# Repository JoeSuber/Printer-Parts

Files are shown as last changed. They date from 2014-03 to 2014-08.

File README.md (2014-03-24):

Printer-Parts
=============

Parts and set-up files for my own functioning 3D-printer design:

Why another 3D printer? Here are the reasons for this one:

1) utilize bargain priced salvaged nema-23 stepper motors, get higher torque/$ and 1/32 micro-steps.

nema-23 motors are mostly bigger, torque-ier, and consequently can draw more current than this job really requires - but they often have a better dollar-per-Newton ratio than the nema-17 motors one usually sees in 3D printers.  I have opportunistically purchased 25 or so for under $10 per and only had to pound the sintered cog-wheel off the shaft to obtain a great, cheap, 4-wire motor. The Pololu stepper drivers that utilize the Texas Instruments chip run cooler and allow 1/32 micro-stepping with a higher top current.  The only downside to that TI driver is a longer minimum pulse than the Allegro chip, but at 1.6 micro-seconds it has never been an issue, even with very small diameters.  Which brings me to the 2nd reason:

2) Get rid of belts and sprockets.

Printed sprockets and mismatched belts are the source of many errors and dreaded backlash.  I think everyone using belts eventually wants to use metal wheels that fit their printer design perfectly.  That cannot help but be another source of expense as we must search out particular diameters, tooth-designs, and shafting. Getting belt tension and return idler wheels to work perfectly without spending for the proper bearings and hardware is another headache we can do without.  The Delta-Bots have shown the wonders of Spectra fishing-line as a transmitter of force. However, I suspect the Delta-Bot works best as a prefab kit - and all the good ones use those carbon-fiber rods which I just don't have laying around. Delta is out. My local hardware store has hobby brass tube that can become 5 or 6 drive-spools for $3.  Idlers can be just about any bearing with some printed cones stuck on the outside to nudge the line on centre.  The headaches don't go away completely, but the diameters are small and the wheels are round. And you learn some fishing knots.

3) direct-drive extruder = fewer headaches, better filament retraction. 

I do eventually want to build a Delta-Bot - they look really neat.  But I suspect the Bowden-tube to the hot-end is not ideal unless filament and PTFE are well-matched and the PTFE is not bulged or worn anywhere along its length.  Also, that PTFE tube is another mail-order-only item.  Sure, I am throwing a lot more mass around by having the extruder motor on the X-carriage, but remember we have the Nema-23 torque and the 5/16 inch diameter drive spool to do the hurky-jerks we need on that mass.  Also, it is cheap and easy to switch between 3mm and 1.75mm filament with this set-up.  The filament drive is chosen to use a 608zz bearing and mk7+ gear, which I think is the best price-performance available.  Wade's + hobbed-bolts don't seem to be worth the extra headaches except to the Rep-Strap purist.

4) Benefit from Prusa-Mendel ubiquity, while avoiding some pitfalls.

This design owes a lot to the Prusa-I3 and Mendel lineage. I think it is naturally stiffer and depending on your skill-set, easier to build.  A low center of gravity and wide base reduce harmonic vibrations.  Y-axis drive is centrally located with no idler. Z-rods are moved off the stepper top-surface so they don't vibro-dance, instead forming a stiffer truss with the 1/4" Z-screw. Canted square-tubes dampen X-wobbles by compressing or tensioning horizontal rods instead of torqueing 90 degree joints.  More of this design is in imperial sizes available at your local North-American Home-Depot or Ace-Hardware.  It isn't as compact, because I like to be able to reach everything.  It isn't as pretty for the same reason.  Aluminium square tube and C-channel are cheaper and easier to cut than maker-beam / t-slot. The smooth-rod lengths are such that you may order 1 long rod, cut it in half (Dremmel, not hacksaw) for each pair.  Linear Bearings are cheap if you stick to LM8UU.  I do believe the LM12UU rod on the Y axis is worth the extra money, as it is acting structurally as well. You have multiple ways to trim and level this as you build. One long 5/16" threaded rod can be cut into all the needed sections, and 1/4" bolts & rod cover most everything else that isn't M3.  Using Sanguinolu as the brains, Marlin Firmware settings for Mendels or Ultimakers will get you most of the way there, just remember to compute the proper (likely much higher) steps - per - millimetre for each axis.  I am not sure why RAMPS 1.x + Arduino Mega2560 are more popular in year 2014 as that combo seems more expensive than Sanguinolu when I add it up - but this design should have no problem using RAMPS or some future ARM based solution which will surely be Prusa-Mendel compatible.

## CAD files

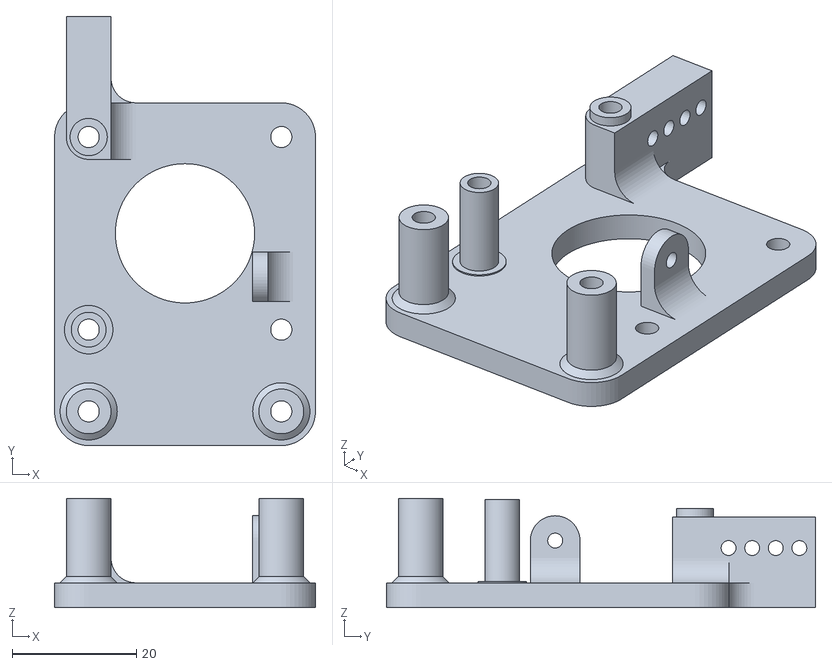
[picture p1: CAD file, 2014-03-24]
ArmDriveSTL/ADBaseMK7.stl
42.0 x 69.0 x 17.6

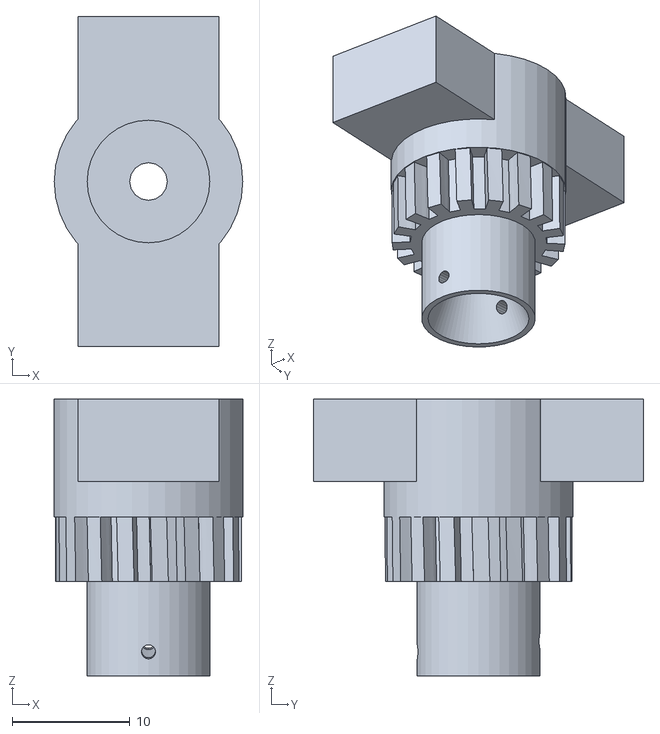
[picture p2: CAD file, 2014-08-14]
x-carriage_thread_plug_14mm.stl
16.0 x 28.0 x 23.5

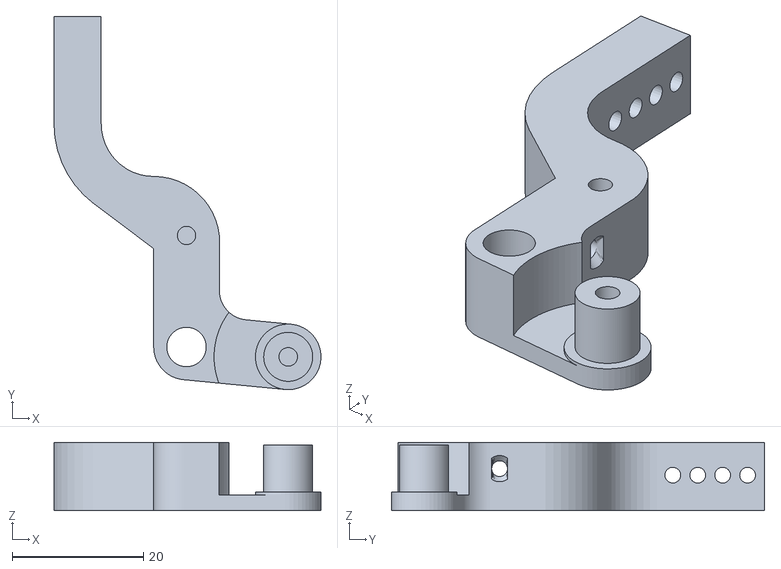
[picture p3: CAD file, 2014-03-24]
ArmDriveSTL/ADLowerArmMK7.stl
40.7 x 56.9 x 10.4

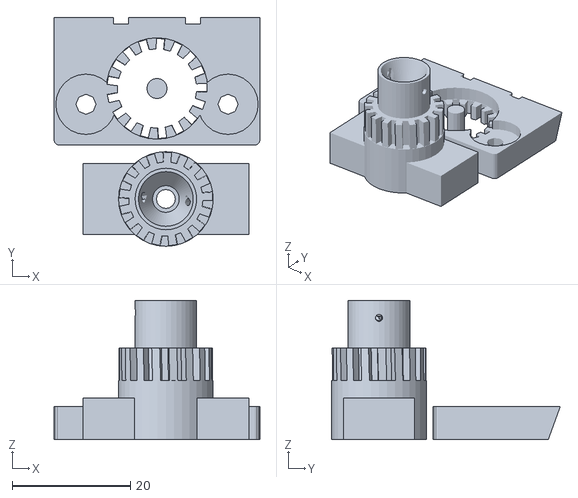
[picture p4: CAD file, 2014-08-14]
x-carriage_thread_plug_hex_only.stl
34.8 x 38.6 x 23.5

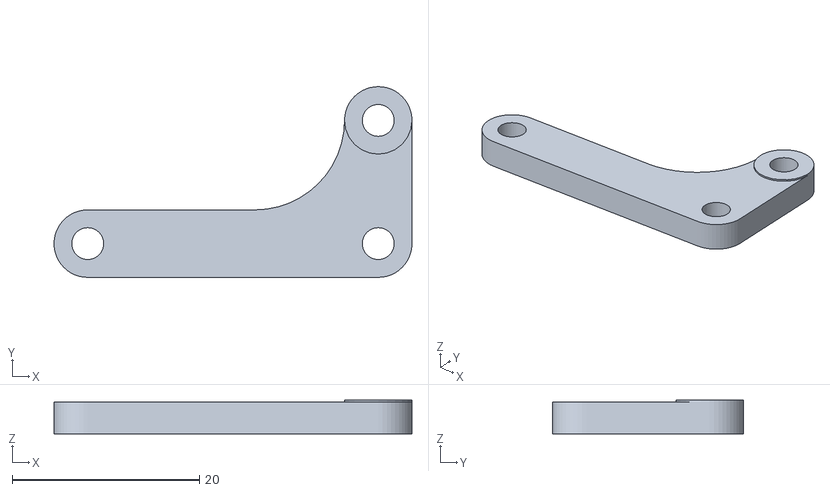
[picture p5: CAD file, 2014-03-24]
ArmDriveSTL/ADTopMK7.stl
38.2 x 20.4 x 3.60

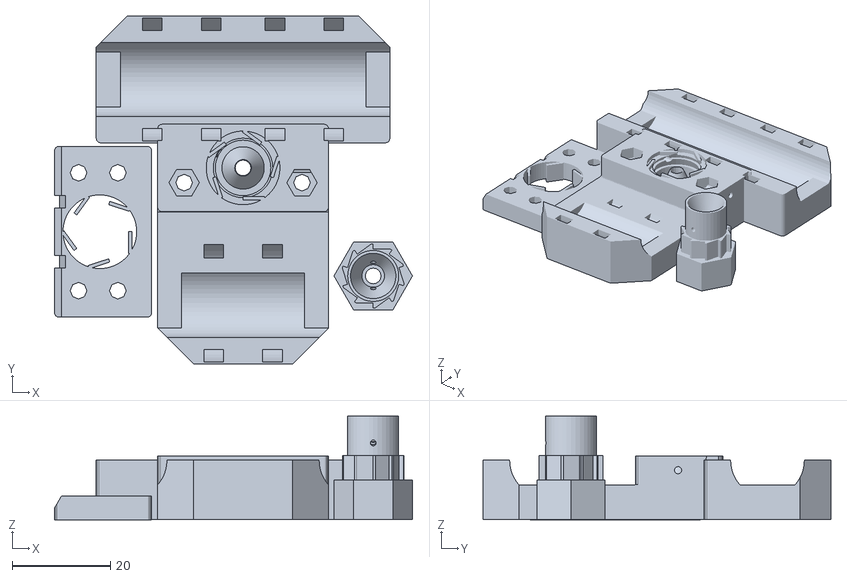
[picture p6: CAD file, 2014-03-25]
x-carriage_for_thread.stl
72.9 x 70.8 x 21.1

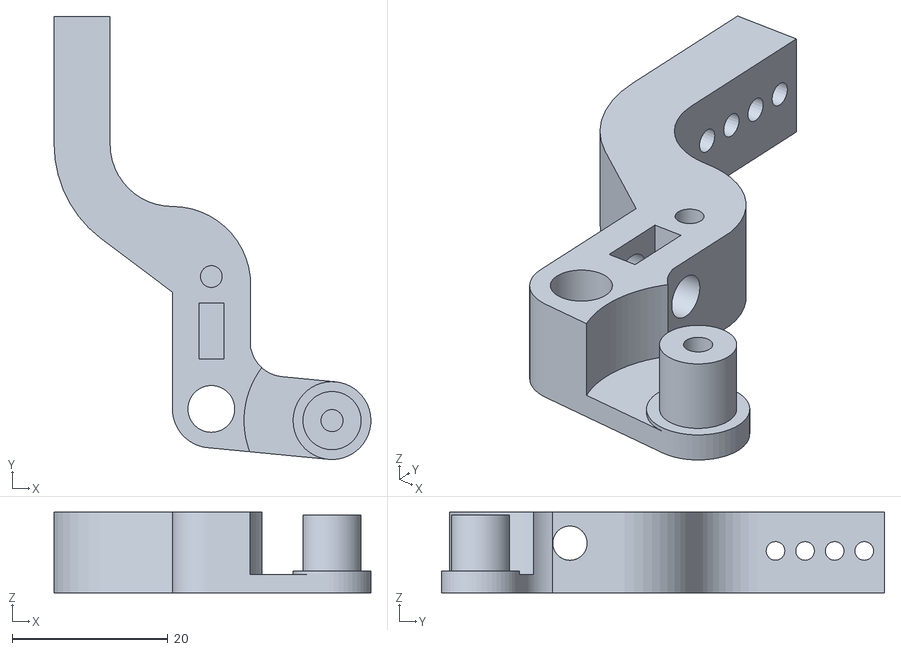
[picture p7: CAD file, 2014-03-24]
ArmDriveSTL/ADLowerArmAltMK7.stl
40.7 x 56.9 x 10.4

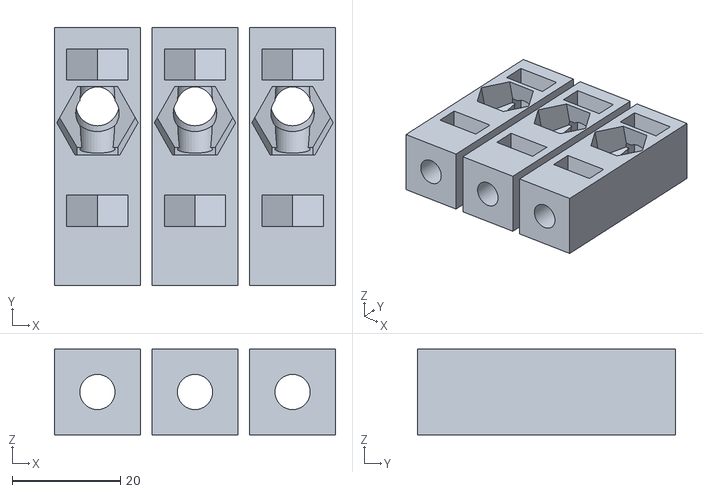
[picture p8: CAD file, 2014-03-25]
bar_rod_joinx2.stl
51.9 x 47.5 x 15.9

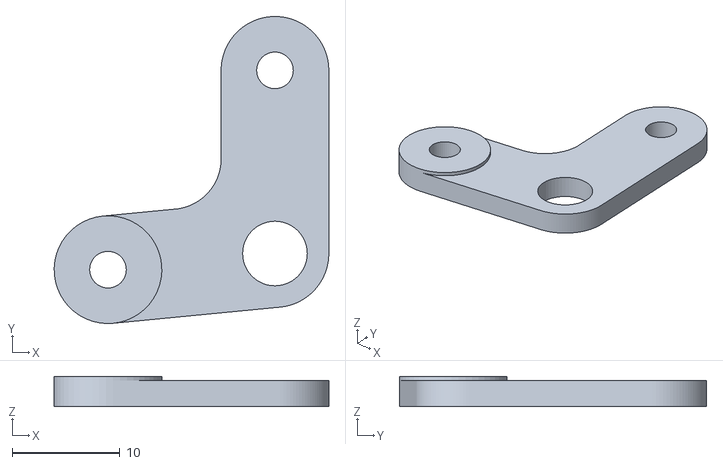
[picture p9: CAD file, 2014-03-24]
ArmDriveSTL/ADUpperArmMK7.stl
25.5 x 28.5 x 2.80

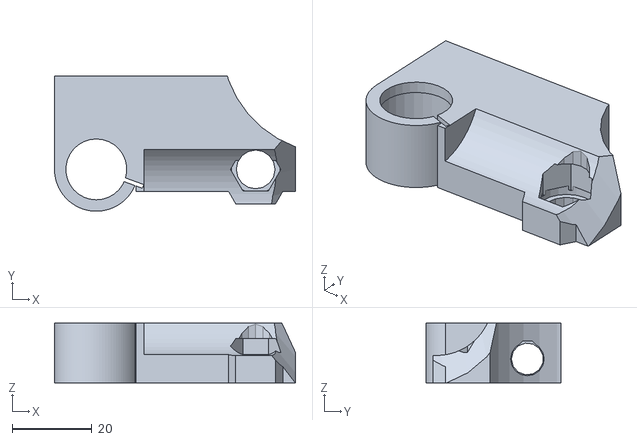
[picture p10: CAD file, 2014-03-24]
top_stabilizer_mirror.stl
60.5 x 34.0 x 15.0

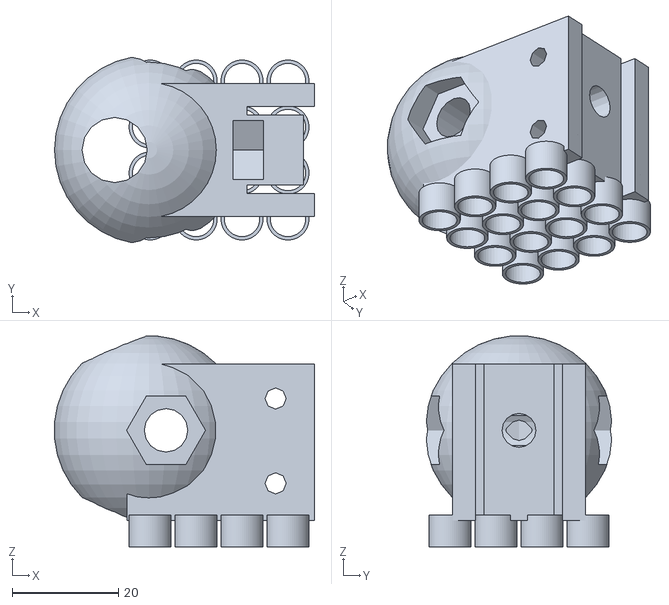
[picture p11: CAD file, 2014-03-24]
bars_bits_on_base.stl
49.0 x 34.9 x 39.8

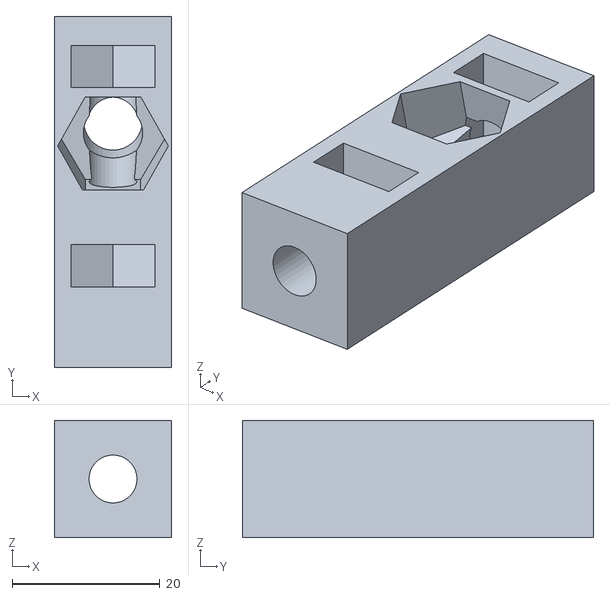
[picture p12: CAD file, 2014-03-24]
bar_to_rod_join.stl
15.8 x 47.5 x 15.9

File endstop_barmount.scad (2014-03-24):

// attach things to base...

use <./Abar.scad>

cB=25;
tubeXY = 19.25;
swX = 20.5;
swY = 10.3;
swZ = 6.5;
wireThick = 3.1;
wireZ = 3.65;
wire1 = 1.11;
wire2 = 11.38;
wire3 = 18.5;
leverHinge = 3.4;
leverExtends = 19.35;
hole1X = 5.15;
hole2X = 14.67;
holeY = 2.78;
holeRad = 2.5/2;
sur = 1.56;
totalX = sur*2 + swX;
totalY = sur + swY;
totalZ = swZ + sur;
posX = totalX/2;
posY = totalY/2 + sur/2;
posZ = totalZ/2;
groove= 1.75;
pH = 30;
Ang = 12.7;

module switch(){
	cube([swX,swY,swZ], center=true);
	translate([0 ,-posY,-.1])
		cube([wire3, 3+2+.1, wireZ+.1], center=true);
}

module switchbox(){
	difference(){
		union(){
		translate([totalX/2,totalY/2,totalZ/2])
			cube([totalX,totalY-.1,totalZ], center=true);			
		}
		translate([posX,posY,posZ])
			switch();
	}
}

module aluTube(){
	cube([tubeXY,tubeXY, pH+.1], center=true);
	translate([tubeXY/2+.1, 0, 0])
		cylinder(r=groove, h=pH+.1, center=true, $fn=16);
	translate([tubeXY/2+.1, tubeXY/3, 0])
		cylinder(r=groove, h=pH+.1, center=true, $fn=16);
	translate([tubeXY/2+.1, -tubeXY/3, 0])
		cylinder(r=groove, h=pH+.1, center=true, $fn=16);
	hull(){
	translate([-tubeXY/2 - sur*2+.2, 0, -pH]) rotate([0,-90,0])
		cylinder(r1=tubeXY/2-2, r2=tubeXY/2+sur*4-2, h=sur*4+.1, center=true);
	translate([-tubeXY/2 - sur*2+.2, 0, pH]) rotate([0,-90,0])
		cylinder(r1=tubeXY/2-2, r2=tubeXY/2+sur*4-2, h=sur*4+.1,center=true);
		}
}

module plasticTube(cH=3){
	minkowski(){
	cube([tubeXY+sur*4,tubeXY+sur, cH], center=true);
	cylinder(r=1.2, h=cH, $fn=48, center=true);
	}

}

module holderclip(){
	difference(){
	plasticTube();
	aluTube();
	}
}

module placeBox(){
	translate([-totalX/2-(pH/2*sin(Ang)-sur-.2),tubeXY,0]) rotate([90,Ang,0])
		switchbox();
}
holderclip();

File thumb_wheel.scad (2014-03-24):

// *******************************************************
// *   Parametric thumb wheel                            *
// *   by Chris Garrett                                  *
// *   20-nov-2011                                       *
// *   Small changes by Juan Gonzalez-Gomez (Obijuan)    *
// *   31-Aug-2012                                       *
// *******************************************************


// *** Configuration variables ***
wheel_d = 12;    // Outer Diameter of the thumb wheel
wheel_h = 3;     // Height of the thumb wheel
hole_d = 3.2;    // Diameter of center hole
hex_sz = 6.4;      // Size of the hex (nut trap)
                 // An M4 nut fits perfectly in a 7mm hex opening made on my Prusa
hex_d = 2;       // Depth of the hex (set this < or = to wheel_h)
knurl_cnt = 8;  // Number of cutouts around the wheel
knurl_d = 3;     // Diameter of the cutouts

//-- drills
drill_M3 = 3.2;

//-- captive Nuts
nut_h = 2.2;
nut_radius = 6.4/2;


// *** Code area ***

// The thumb wheel 

difference() {
  //-- Base cylinder
  cylinder(h=wheel_h, r=wheel_d/2, $fn=50);

  //-- Cutouts
  for(i = [0:knurl_cnt-1]) {
   rotate(v=[0,0,1], a=i*360/knurl_cnt) 
     translate([0,wheel_d/2+knurl_d/4,-1]) 
       cylinder(h=wheel_h+2, r=knurl_d/2, $fn=50);
  }

  //-- Hex nut body
  translate([0,0,wheel_h-nut_h])
    cylinder(r=nut_radius, h=nut_h+1,$fn=6);

  //-- Hex nut drill
  translate([0,0,-1]) cylinder(h=wheel_h+2, r=hole_d/2, $fn=50);

}

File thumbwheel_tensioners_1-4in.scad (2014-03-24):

include </home/suber1/MCAD/gears.scad>

spread = 12;
teeth = 23;
dp = 1.1;
pi = 3.141592654;
crad = (teeth*dp/pi)/2;
pad = 0.1;	// Padding to maintain manifold
ch = 1;
cr = 17.5;
ct = 2;
r = 3.15;
smooth = 64;	// Number of facets of rounding cylinder

module toroid(){
//difference() {
//	rotate_extrude(convexity=10,  $fn = smooth)
//		translate([cr-ct-r+pad,ct-pad,0])
//			square(r+pad,r+pad);
	rotate_extrude(convexity=10,  $fn = smooth)
		translate([cr-ct-r,ct+r,0])
			circle(r=r,$fn=smooth);
//}
}

module wind_ring(){
difference(){
cylinder(r = crad*2+4, h=2,center=true, $fn=48);
cylinder(r = crad*2+4-2.4, h=2, center=true, $fn=36);
}
}



module thumbwheel(){
difference(){translate([0,0,5]) linear_extrude(height = 8.5, center = true, convexity = 10, twist = 0)
	 //gear(number_of_teeth=21,diametral_pitch=1);
gear(teeth, diametral_pitch=dp, presure_angle=20, clearance=.275);
translate([0,0,5]) rotate([0,90,90]);
	cylinder(r=.66, h= 20, $fn=12, center=true);
translate([0,0,-10]) rotate([180,0,0]);
toroid();
translate([0,0,0]) rotate([0,180,0]);
toroid();
translate([0,0,6.5])
cylinder(r=6.59, h= 6.5, $fn=6, center=true);
//translate([0,0,6])
//wind_ring();
translate([0,0,7])
	cylinder(r=3.25, h= 20, $fn=36, center=true);
// threadhole
translate([0,0,5]) rotate([0,90,90]);
	cylinder(r=.66, h= 20, $fn=12, center=true);
}
}
module fourthumbs(){
rotate([0,180,0]) translate([spread,spread,0])
	thumbwheel();
rotate([0,180,0]) translate([spread,-spread,0])
	thumbwheel();
rotate([0,180,0]) translate([-spread,spread,0])
	thumbwheel();
rotate([0,180,0]) translate([-spread,-spread,0])
	thumbwheel();
}


echo("teeth*pitch/pi/2 =",crad);
fourthumbs();

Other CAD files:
thumbwheels.scad
3_8_to_5_16_inserts.scad
Abar.scad
Alum_Cchan1633x1266.scad
BottomBlock.scad
BottomBlock_top_plate_solo.scad
RatchetLib.scad
SpringSwivvel_LM12UU.scad
SpringSwivvel_LM8UU_3rd.scad
bar_rod_joinx2.scad
bar_to_rod_join.scad
bar_to_rod_longie.scad
bars_bits_on_base.scad
bars_n_bits.scad
bars_n_bits_x3.scad
bars_n_bits_x4.scad
bearing.scad
cylinders.scad
drill_guide_for_alum.scad
endstop_on_C_bar.scad
endstop_ontubeclip.scad
external_gear_script.scad
polyholes.scad
spool_4_shells.scad
spool_idler_x.scad
top_stabilizers.scad
wiremanage_tubeclip.scad
x-carriage_for_thread.scad
x-carriage_thread_plug.scad
x-carriage_thread_plug_14mm.scad
x-carriage_thread_plug_hex_only.scad
x-end-idler.scad
x-end-motor.scad
x-end.scad

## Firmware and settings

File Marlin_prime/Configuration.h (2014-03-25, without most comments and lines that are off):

#define CONFIGURATION_H
#define STRING_VERSION_CONFIG_H __DATE__ "March15-2014 " __TIME__ // build date and time
#define STRING_CONFIG_H_AUTHOR "Joe Suber" // Who made the changes.
#define SERIAL_PORT 0
#define BAUDRATE 250000
#define MOTHERBOARD 62
#define EXTRUDERS 1
#define POWER_SUPPLY 1
#define TEMP_SENSOR_0 1
#define TEMP_SENSOR_1 0
#define TEMP_SENSOR_2 0
#define TEMP_SENSOR_BED 1
#define MAX_REDUNDANT_TEMP_SENSOR_DIFF 10
#define TEMP_RESIDENCY_TIME 10  // (seconds)
#define TEMP_HYSTERESIS 3       // (degC) range of +/- temperatures considered "close" to the target one
#define TEMP_WINDOW     1       // (degC) Window around target to start the residency timer x degC early.
#define HEATER_0_MINTEMP 5
#define HEATER_1_MINTEMP 5
#define HEATER_2_MINTEMP 5
#define BED_MINTEMP 5
#define HEATER_0_MAXTEMP 248
#define HEATER_1_MAXTEMP 275
#define HEATER_2_MAXTEMP 275
#define BED_MAXTEMP 130
#define PIDTEMP
#define BANG_MAX 255 // limits current to nozzle while in bang-bang mode; 255=full current
#define PID_MAX 255 // limits current to nozzle while PID is active (see PID_FUNCTIONAL_RANGE below); 255=full current
  #define PID_FUNCTIONAL_RANGE 10 // If the temperature difference between the target temperature and the actual temperature
  #define PID_INTEGRAL_DRIVE_MAX 255  //limit for the integral term
  #define K1 0.95 //smoothing factor within the PID
  #define PID_dT ((OVERSAMPLENR * 8.0)/(F_CPU / 64.0 / 256.0)) //sampling period of the temperature routine
    #define  DEFAULT_Kp 22.2
   #define  DEFAULT_Ki 1.08
    #define  DEFAULT_Kd 114
#define MAX_BED_POWER 255 // limits duty cycle to bed; 255=full current
#define ENDSTOPPULLUPS // Comment this out (using // at the start of the line) to disable the endstop pullup resistors
  #define ENDSTOPPULLUP_XMAX
  #define ENDSTOPPULLUP_YMAX
  #define ENDSTOPPULLUP_ZMAX
  #define ENDSTOPPULLUP_XMIN
  #define ENDSTOPPULLUP_YMIN
  #define ENDSTOPPULLUP_ZMIN
const bool X_MIN_ENDSTOP_INVERTING = false; // set to true to invert the logic of the endstop.
const bool Y_MIN_ENDSTOP_INVERTING = false; // set to true to invert the logic of the endstop.
const bool Z_MIN_ENDSTOP_INVERTING = false; // set to true to invert the logic of the endstop.
const bool X_MAX_ENDSTOP_INVERTING = false; // set to true to invert the logic of the endstop.
const bool Y_MAX_ENDSTOP_INVERTING = false; // set to true to invert the logic of the endstop.
const bool Z_MAX_ENDSTOP_INVERTING = false; // set to true to invert the logic of the endstop.
#if defined(COREXY) && !defined(DISABLE_MAX_ENDSTOPS)
  #define DISABLE_MAX_ENDSTOPS
#endif
#define X_ENABLE_ON 0
#define Y_ENABLE_ON 0
#define Z_ENABLE_ON 0
#define E_ENABLE_ON 0 // For all extruders
#define DISABLE_X false
#define DISABLE_Y false
#define DISABLE_Z false
#define DISABLE_E false // For all extruders
#define INVERT_X_DIR true    // for Mendel set to false, for Orca set to true
#define INVERT_Y_DIR false    // for Mendel set to true, for Orca set to false
#define INVERT_Z_DIR false     // for Mendel set to false, for Orca set to true
#define INVERT_E0_DIR true   // for direct drive extruder v9 set to true, for geared extruder set to false
#define INVERT_E1_DIR false    // for direct drive extruder v9 set to true, for geared extruder set to false
#define INVERT_E2_DIR false   // for direct drive extruder v9 set to true, for geared extruder set to false
#define X_HOME_DIR 1
#define Y_HOME_DIR -1
#define Z_HOME_DIR 1
#define min_software_endstops true // If true, axis won't move to coordinates less than HOME_POS.
#define max_software_endstops true  // If true, axis won't move to coordinates greater than the defined lengths below.
#define X_MAX_POS 220
#define X_MIN_POS 0
#define Y_MAX_POS 170
#define Y_MIN_POS 0
#define Z_MAX_POS 120
#define Z_MIN_POS 0
#define X_MAX_LENGTH (X_MAX_POS - X_MIN_POS)
#define Y_MAX_LENGTH (Y_MAX_POS - Y_MIN_POS)
#define Z_MAX_LENGTH (Z_MAX_POS - Z_MIN_POS)
#define MANUAL_X_HOME_POS 0
#define MANUAL_Y_HOME_POS 0
#define MANUAL_Z_HOME_POS 0
#define NUM_AXIS 4 // The axis order in all axis related arrays is X, Y, Z, E
#define HOMING_FEEDRATE {50*60, 50*60, 4*60, 0}  // set the homing speeds (mm/min)
#define DEFAULT_AXIS_STEPS_PER_UNIT   {256.65301, 115.749, 5039.37, 209.0}   // steps per unit for Joe-Bot X, Y, Z, E
#define DEFAULT_MAX_FEEDRATE          {500, 500, 4, 25}    // (mm/sec)
#define DEFAULT_MAX_ACCELERATION      {9000,9000,100,10000}    // X, Y, Z, E maximum start speed for accelerated moves. E default values are good for Skeinforge 40+, for older versions raise them a lot.
#define DEFAULT_ACCELERATION          3000    // X, Y, Z and E max acceleration in mm/s^2 for printing moves
#define DEFAULT_RETRACT_ACCELERATION  3000   // X, Y, Z and E max acceleration in mm/s^2 for retracts
#define DEFAULT_XYJERK                20.0    // (mm/sec)
#define DEFAULT_ZJERK                 0.4     // (mm/sec)
#define DEFAULT_EJERK                 5.0    // (mm/sec)
#define EEPROM_CHITCHAT
#define PLA_PREHEAT_HOTEND_TEMP 180
#define PLA_PREHEAT_HPB_TEMP 70
#define PLA_PREHEAT_FAN_SPEED 255   // Insert Value between 0 and 255
#define ABS_PREHEAT_HOTEND_TEMP 240
#define ABS_PREHEAT_HPB_TEMP 100
#define ABS_PREHEAT_FAN_SPEED 255   // Insert Value between 0 and 255
#define SOFT_PWM_SCALE 0
#include "Configuration_adv.h"
#include "thermistortables.h"

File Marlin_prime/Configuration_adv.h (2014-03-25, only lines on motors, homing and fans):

#define CONTROLLERFAN_PIN -1 //Pin used for the fan to cool controller (-1 to disable)
#define EXTRUDER_0_AUTO_FAN_PIN -1
#define EXTRUDER_1_AUTO_FAN_PIN -1
#define EXTRUDER_2_AUTO_FAN_PIN -1
#define ENDSTOPS_ONLY_FOR_HOMING // If defined the endstops will only be used for homing
#define X_HOME_RETRACT_MM 5
#define Y_HOME_RETRACT_MM 5
#define Z_HOME_RETRACT_MM 1
#define MICROSTEP1 LOW,LOW
#define MICROSTEP2 HIGH,LOW
#define MICROSTEP4 LOW,HIGH
#define MICROSTEP8 HIGH,HIGH
#define MICROSTEP16 HIGH,HIGH
#define MICROSTEP_MODES {16,16,16,16,16} // [1,2,4,8,16]
#define DIGIPOT_MOTOR_CURRENT {135,135,135,135,135} // Values 0-255 (RAMBO 135 = ~0.75A, 185 = ~1A)
#define DIGIPOT_I2C_MOTOR_CURRENTS {1.0, 1.0, 1.0, 1.0, 1.0, 1.0, 1.0, 1.0}

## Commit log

2014-03-24 OpenScad files to and some STL for printable parts for JoePrint
    [3_8_to_5_16_inserts.scad, ADBaseMK7.stl, ADLowerArmAltMK7.stl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]
2014-03-25 adding Marlin firmware and some stray parts
    [Configuration.h, Configuration_adv.h, bar_rod_joinx2.stl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]
2014-08-14 update the z-travel and new x-carriage thread tensioner
    [x-carriage_thread_plug_14mm.scad, x-carriage_thread_plug_14mm.stl, x-carriage_thread_plug_hex_only.stl]
